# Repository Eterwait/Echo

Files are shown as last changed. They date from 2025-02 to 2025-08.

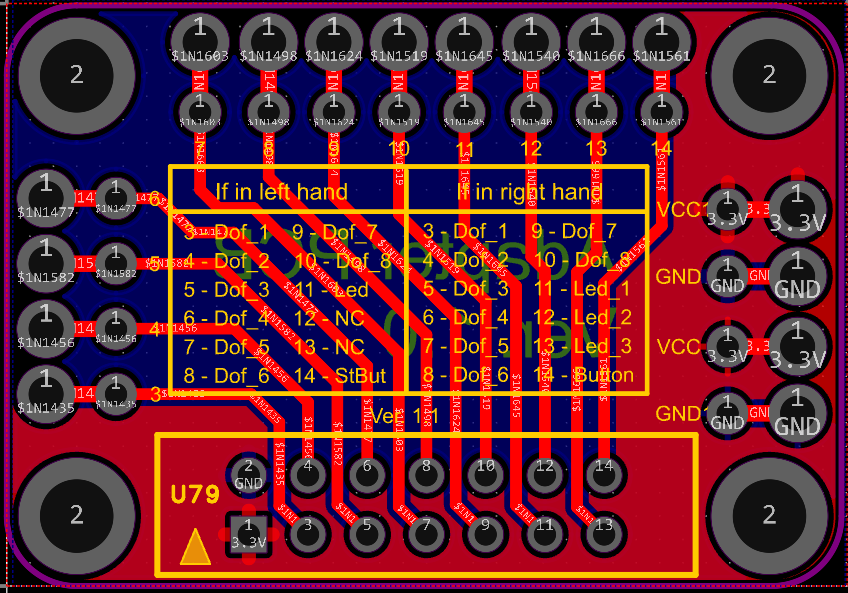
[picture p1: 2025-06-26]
Hardware/Commutation/Adapter_1.0/Adapter_1.0_schematic.PNG

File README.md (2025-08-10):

## Welcome to Echo!
This repository contains source materials for Echo, an open-source teleoperation system with force feedback.

Feel free to visit our [website](https://eterwait.github.io/Echo/) for more information!

### Repository content

- **Echo** - main code.
- **Hardware** - 3D models and electronic components.
- **STM32 code** - STM32 CubeIDE project files.
- **force_sensor_linearizer_rs485** - force sensor PCB code
- **Echo.bin** - ready-to-use microcontroller firmware. Download [Cube Programmer](https://www.st.com/en/development-tools/stm32cubeprog.html) and use it to upload the firmware to the board.
- **Echo.hex** - ready-to-use microcontroller firmware.

### Hardware & Assembly Tutorial

Echo is easy to put together with our [Hardware & Assembly Tutorial](https://eterwait.github.io/Echo/Hardware) videos and guide. Check it out to get started!

### Citation

```
@misc{bazhenov2025echoopensourcelowcostteleoperation,
      title={Echo: An Open-Source, Low-Cost Teleoperation System with Force Feedback for Dataset Collection in Robot Learning}, 
      author={Artem Bazhenov and Sergei Satsevich and Sergei Egorov and Dzmitry Tsetserukou},
      year={2025},
      eprint={2504.07939},
      archivePrefix={arXiv},
      primaryClass={cs.RO},
      url={https://arxiv.org/abs/2504.07939}, 
}
```

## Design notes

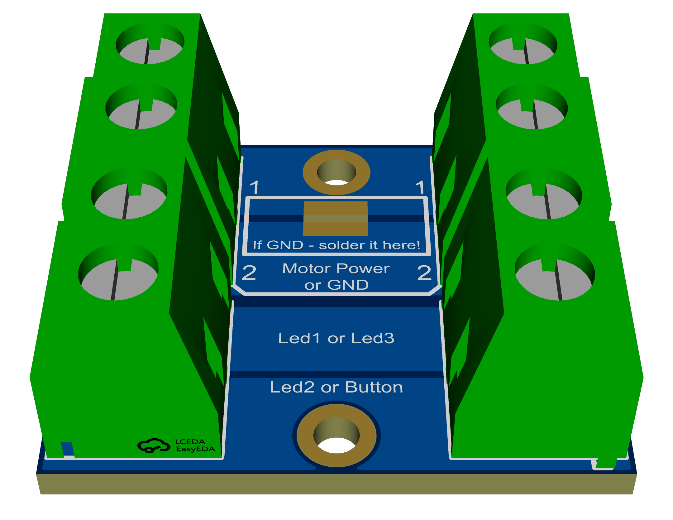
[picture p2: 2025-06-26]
Hardware/Commutation/Commutation_hand_1.0/Commutation_hand_1.0_side_view.png

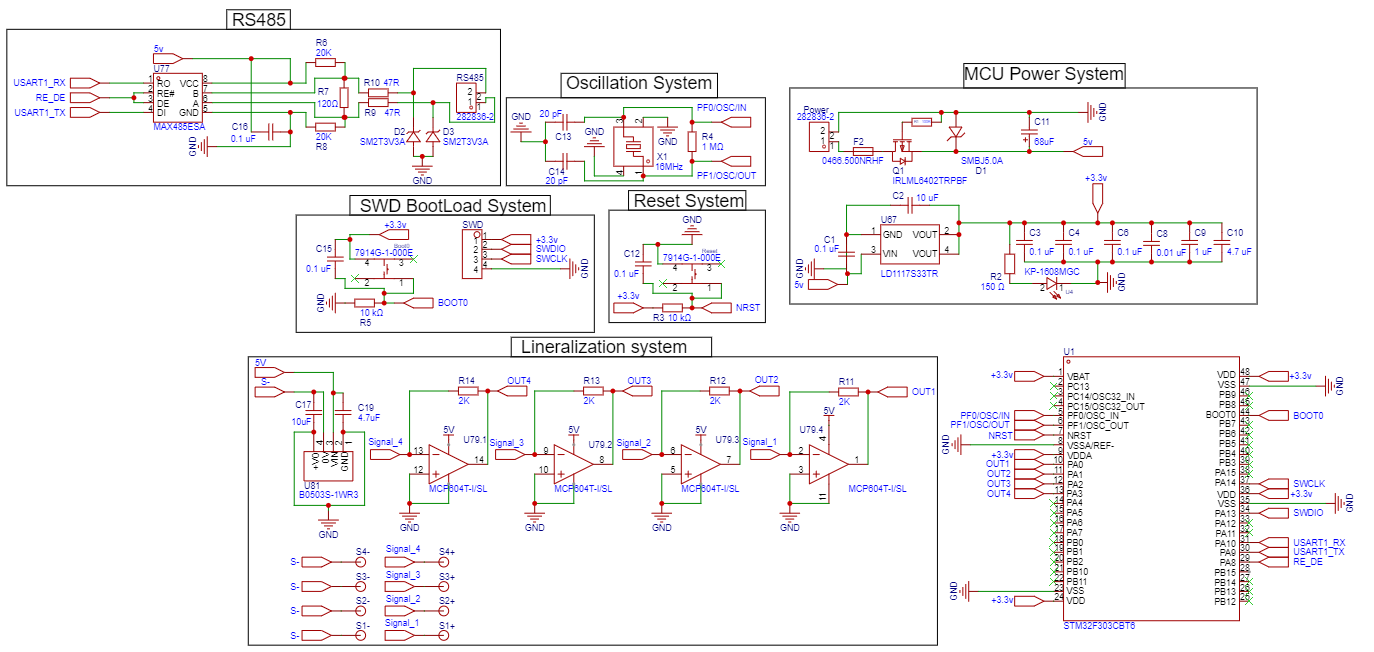
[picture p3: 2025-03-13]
Hardware/Force sensor PCB/Force sensor Schematics.png

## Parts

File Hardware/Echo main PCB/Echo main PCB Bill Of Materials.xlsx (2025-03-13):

No. | Vendor | Link | Device | Footprint | Quantity | Comment | Designator | Secondary Category | Name | Russian/Chinese Vendors | Link | Price rub
1 | DigiKey | https://www.digikey.com/en/products/detail/bourns-inc/7914G-1-000E/158358 | 7914G-1-000E | KEY-SMD_4P-L5.0-W5.0-P2.54-LS5.5-BL | 3 | 7914G-1-000E | Boot0,Boot1,Reset | Tactile Switches | 7914G-1-000E | chipdip | https://www.chipdip.ru/product/7914g-1-000 | 320
2 | Ali-Express | https://aliexpress.ru/item/1005004452143266.html?sku_id=12000029224903107 | GMD12095YB-3.3V | BUZ-TH_BD12.0-P7.60-D0.6-FD | 1 | GMD12095YB-3.3V | BUZZER | Buzzers | GMD12095YB-3.3V | Ali-Express | https://aliexpress.ru/item/1005004452143266.html?sku_id=12000029224903107 | 117
3 | Mouser | https://www.mouser.com/ProductDetail/Vishay-Vitramon/VJ0603Y104KXJAP | CAP_0603 GRM188R71H104JA93D | C0603 | 2 | 0.1 uF 16v | C1,C60 | Ceramic Capacitors MLCC - SMD/SMT | 0.1 uF 16v | chipdip | https://www.chipdip.ru/product/grm188r71h104ja93d | 6
4 | Mouser | https://www.mouser.com/ProductDetail/KYOCERA-AVX/TAJE227K016RNJ?qs=fdqkYiOtZpcgegJ8JKuPSw%3D%3D | TAJE227K016RNJ | CASE-E_7343 | 2 | 220 uF 16v | C2,C3 | Tantalum Capacitors | 220 uF 16v | chipdip | https://www.chipdip.ru/product/taje227k016rnj-avx | 250
5 | Mouser | https://www.mouser.com/ProductDetail/KYOCERA-AVX/TAJB226K016RNJ?qs=mgX5NEyWO4SD2hYJZOOvhw%3D%3D | TAJB226K016RNJ | CASE-B_3528 | 1 | 22 uF 10v | C4 | Tantalum Capacitors | 22 uF 10v | chipdip | https://www.chipdip.ru/product/tecap-22-mkf-16-v-tip-b-10 | 44
6 | Mouser | https://www.mouser.com/ProductDetail/KEMET/C0603X104K8RACTU | CAP_0603 GRM188R71H104JA93D | C0603 | 32 | 0.1 uF 10v | C5,C10,C11,C12,C13,C14,C18,C19,C20,C26,C27,C28,C29,C30,C31,C32,C33,C34,C35,C36,C37,C38,C39,C40,C41,C42,C43,C44,C51,C52,C68,C69 | Ceramic Capacitors MLCC - SMD/SMT | 0.1 uF 10v | chipdip | https://www.chipdip.ru/product/grm188r71h104ja93d | 6
7 | Mouser | https://www.mouser.com/ProductDetail/Murata-Electronics/GRM188R61A475KAAJD?qs=mJtAphxf33RijE30dSir3g%3D%3D | CAP_0603 GRM188R61A475K | C0603 | 2 | 4.7 uF 10v | C6,C66 | Ceramic Capacitors MLCC - SMD/SMT | 4.7 uF 10v | chipdip | https://www.chipdip.ru/product0/9000193550 | 15
8 | Mouser | https://www.mouser.com/ProductDetail/TDK/C1608X7R1A106M080AT | CAP_0603 GRM188Z71A106KA73D | C0603 | 1 | 10 uF 10v | C9 | Ceramic Capacitors MLCC - SMD/SMT | 10 uF 10v | chipdip | https://www.chipdip.ru/product0/9000502859 | 8
9 | Mouser | https://www.mouser.com/ProductDetail/KEMET/C0603C200K8HACTU?qs=W0yvOO0ixfG41DXbAfv7cA%3D%3D | CAP_0603 | C0603 | 2 | 20 pF 10v | C16,C17 | Ceramic Capacitors MLCC - SMD/SMT | 20 pF 10v | chipdip | https://www.chipdip.ru/product/grm1885c1h200j | 7
10 | Mouser | https://www.mouser.com/ProductDetail/Vishay-Sprague/293D104X9035A2TE3?qs=wgO0AD0o1vu82gSB7jpq2A%3D%3D | CAP_0603 293D104X9035A2TE3 | C0603,CASE-A_3216 | 4 | 0,1 uF 16v | C46,C47,C54,C55 | Tantalum Capacitors | 0,1 uF 16v | chipdip | https://www.chipdip.ru/product0/1654 | 32
11 | Newark | https://www.newark.com/kemet/c0603c224j4ractu/cap-0-22-f-16v-5-x7r-0603/dp/94Y9862 | CAP_0603 | C0603 | 2 | CBoot_0,22uF 16v | C48,C56 | Ceramic Capacitors MLCC - SMD/SMT | CBoot_0,22uF 16v | chipdip | https://www.chipdip.ru/product0/8013249347 | 2
12 | Newark | https://www.newark.com/kemet/c0603c103k4hactu/cap-0-01uf-16v-mlcc-0603-rohs/dp/66AJ6963 | CAP_0603 | C0603 | 2 | 0,01 uF 16v | C49,C57 | Ceramic Capacitors MLCC - SMD/SMT | 0,01 uF 16v | chipdip | https://www.chipdip.ru/product0/8022330951 | 5
13 | Newark | https://www.newark.com/murata/grm033r71a562ka01d/cap-5600pf-10v-mlcc-0201/dp/97AH9613 | CAP_0603 | C0603 | 2 | 5.6 nF 10v | C50,C58 | Ceramic Capacitors MLCC - SMD/SMT | 5.6 nF 10v | chipdip | https://www.chipdip.ru/product/grm188r71h562k | 7
14 | Newark | https://www.newark.com/murata/grm188c81c106ma73j/cap-10uf-16v-mlcc-0603-rohs-compliant/dp/64AJ4361 | CAP_0603 | C0603 | 1 | 10 uF 16v | C59 | Ceramic Capacitors MLCC - SMD/SMT | 10 uF 16v | chipdip | https://www.chipdip.ru/product0/9000388115 | 6
15 | Newark | https://www.newark.com/yageo/cc0603krx7r6bb104/cap-0-1uf-10v-mlcc-0603-rohs-compliant/dp/26AK1888 | CAP_0603 | C0603 | 4 | 0.1uF 10v | C61,C62,C63,C64 | Ceramic Capacitors MLCC - SMD/SMT | 0.1uF 10v | chipdip | https://www.chipdip.ru/product0/8005306866 | 29
16 | Newark | https://www.newark.com/kemet/c0603c105z8vactu/cap-1-f-10v-y5v-0603/dp/76Y2908 | CAP_0603 | C0603 | 1 | 1 uF 10v | C67 | Ceramic Capacitors MLCC - SMD/SMT | 1 uF 10v | chipdip | https://www.chipdip.ru/product/gcm188r71e105ka64d-murata | 28
17 | Ali-Express | https://aliexpress.ru/item/32878041549.html?sku_id=65528795603 | XT30PW-M30.G.Y | CONN-TH_XT30PW-M | 1 | XT30PW-M30.G.Y | CN1 | plug | XT30PW-M30.G.Y | Ali-Express | https://aliexpress.ru/item/32878041549.html?sku_id=65528795603 | 1200 | Total price rub:
18 | Mouser | https://www.mouser.com/ProductDetail/Bourns/SMCJ16A?qs=%252Bf8Cd6aE5byqCW8Yyl7Q2g%3D%3D | SMCJ16A_C310019 | SMC_L6.9-W5.9-LS7.9-RD | 1 | SMCJ16A | D1 | ESD and Surge Protection (TVS/ESD) | SMCJ16A | chipdip | https://www.chipdip.ru/product0/8011003304 | 140 | 11527
19 | Mouser | https://www.mouser.com/ProductDetail/STMicroelectronics/SM2T3V3A?qs=SoAZXCQuyY%2F4L%252BcP08CfZA%3D%3D | SM2T3V3A | DO-216AA_L1.9-W1.9-LS3.8-FD | 4 | SM2T3V3A | D3,D4,D5,D6 | TVS | SM2T3V3A | chipdip | https://www.chipdip.ru/product/sm2t3v3a-stm | 160
20 | Mouser | https://www.mouser.com/ProductDetail/Panjit/1N4148W_R1_00001?qs=sPbYRqrBIVnqVztCqPNVrw%3D%3D | 1N4148W_C143180 | SOD-123FL_L2.7-W1.6-LS3.8-RD | 4 | 1N4148W | D7,D8,D9,D10 | Switching Diodes | 1N4148W | chipdip | https://www.chipdip.ru/product/1n4148w-2 | 3
21 | Mouser | https://www.mouser.com/ProductDetail/Texas-Instruments/TPD2EUSB30DRTR?qs=%2Fqzd9s%252BcLd6bPJi5HXCDvw%3D%3D | TPD2EUSB30DRTR-TP | SOT-723-3_L1.2-W0.8-LS1.20-BR | 1 | TPD2EUSB30DRTR-TP | D15 | ESD and Surge Protection (TVS/ESD) | TPD2EUSB30DRTR-TP | chipdip | https://www.chipdip.ru/product0/8010090243 | 13
22 | Mouser | https://www.mouser.com/ProductDetail/Comchip-Technology/SS510-HF?qs=GBLSl2AkirsMVpU1ZRGkfw%3D%3D | SS510_C106905 | SMA_L4.4-W2.8-LS5.4-RD | 1 | SS510 | D16 | Schottky Diodes | SS510 | chipdip | https://www.chipdip.ru/product/ss510-umw | 11
23 | Ali-Express | https://aliexpress.ru/item/4001283958345.html?sku_id=12000043098655572 | HDR-M_2.54_1x4P | HDR-TH_4P-P2.54-V-M | 1 | HDR-M_2.54_1x4P | H1 | Pin Headers |  | Ali-Express | https://aliexpress.ru/item/4001283958345.html?sku_id=12000043098655572 | 63
24 | LCSC | https://www.lcsc.com/product-detail/IDC-Connectors_Ckmtw-Shenzhen-Cankemeng-B-3100S14P-A110_C146651.html | B-3100S14P-A110 | IDC-TH_310S-14P | 2 | B-3100S14P-A110 | Left_ADC,Right_ADC | IDC Connectors | B-3100S14P-A110 | chipdip | https://www.chipdip.ru/product/idcc-14ms | 26
25 | Mouser | https://www.mouser.com/ProductDetail/SparkFun/PRT-08432?qs=WyAARYrbSnYz%2FplK2qCI8A%3D%3D | 282836-2 | Screw terminal block 2-pin, 5mm CONN-TH_2P-P5.00_282836-2 | 6 | 282836-2 | Left_Motor_Power,POWER,POWER,Right_Motor_Power,RS485,RS485_2 | Screw Terminal Blocks | 282836-2 | chipdip | https://www.chipdip.ru/product/tyco-282836-2 | 80
26 | Newark | https://www.newark.com/tdk/mpz1608y151btd25/chip-bead-aec-q200-150-ohm-0603/dp/50AJ4286 | ERJ6ENF2053V,Res_0603 | R0603 | 5 | 150R | R1,R33,R34,R35,R49 | Chip Resistor - Surface Mount | 150R | chipdip | https://www.chipdip.ru/product0/8043206677 | 2
27 | Newark | https://www.newark.com/vishay/crcw06031m00fkta/res-thick-film-1m-1-0-1w-0603/dp/66F9077 | Res_0603 | R0603 | 1 | 1M | R2 | Chip Resistor - Surface Mount | 1M | chipdip | https://www.chipdip.ru/product/0.1w-0603-1-mom-1 | 6
28 | Newark | https://www.newark.com/vishay/crcw060310k0fkta/res-10k-1-0-1w-0603-thick-film/dp/22AC8032 | Res_0603 | R0603 | 7 | 10K | R3,R4,R5,R36,R38,R39,R41 | Chip Resistor - Surface Mount | 10K | chipdip | https://www.chipdip.ru/product/0.1w-0603-10-kom-5 | 6
29 | Newark | https://www.newark.com/yageo/rc0603fr-0720kl/res-20k-1-0-1w-0603-thick-film/dp/82AH8092 | Res_0603 | R0603 | 2 | 20K | R12,R14 | Chip Resistor - Surface Mount | 20K | chipdip | https://www.chipdip.ru/product/0.1w-0603-20-kom-1 | 6
30 | Newark | https://www.newark.com/murata/blm31pg121sn1l/ferrite-bead-120r-3-5a-1206/dp/02AC3396 | 1206W4J0121T5E | R1206 | 1 | 120R | R13 | Chip Resistor - Surface Mount | 120R | chipdip | https://www.chipdip.ru/product/0.25w-1206-120-om-1 | 6
31 | Newark | https://www.newark.com/vishay/crcw060347r0fkea/res-thick-film-47r-1-0-1w-0603/dp/72M6842 | Res_0603 | R0603 | 2 | 47R | R15,R16 | Chip Resistor - Surface Mount | 47R | chipdip | https://www.chipdip.ru/product/0.1w-0603-47-om-1 | 6
32 | Newark | https://www.newark.com/vishay/crcw060310r0jnea/res-thick-film-10r-5-0-1w-0603/dp/59M6762 | Res_0603 | R0603 | 16 | 10R | R17,R18,R19,R20,R21,R22,R23,R24,R25,R26,R27,R28,R29,R30,R31,R32 | Chip Resistor - Surface Mount | 10R | chipdip | https://www.chipdip.ru/product/0.1w-0603-10-om-1 | 6
33 | Newark | https://www.newark.com/vishay/crcw0603100rfkta/res-thick-film-100r-1-0-1w-0603/dp/66F9065 | Res_0603 | R0603 | 2 | 100R | R37,R40 | Chip Resistor - Surface Mount | 100R | chipdip | https://www.chipdip.ru/product/0.1w-0603-100-om-1 | 6
34 | Newark | https://www.newark.com/yageo/rt0603drd075k1l/res-5k1-0-5-0-1w-0603-thin-film/dp/82AH8969 | Res_0603 | R0603 | 1 | 5,1K | R42 | Chip Resistor - Surface Mount | 5,1K | chipdip | https://www.chipdip.ru/product/0.1w-0603-5.1-kom-1 | 6
35 | Newark | https://www.newark.com/te-connectivity/cpf0603b24re1/surface-mount-thin-film-resistor/dp/95W6640 | Res_0603 | R0603 | 4 | 24R | R43,R44,R45,R46 | Chip Resistor - Surface Mount | 24R | chipdip | https://www.chipdip.ru/product/0.1w-0603-24-om-1 | 6
36 | Newark | https://www.newark.com/vishay/crcw0603330rjnea/res-thick-film-330r-5-0-1w-0603/dp/59M6805 | Res_0603 | R0603 | 1 | 330R | R47 | Chip Resistor - Surface Mount | 330R | chipdip | https://www.chipdip.ru/product/0.1w-0603-330-om-1 | 6
37 | Newark | https://www.newark.com/vishay/rca06031k00fkea/res-aec-q200-thick-film-1k-1-0603/dp/98Y2317 | Res_0603 | R0603 | 1 | 1K | R48 | Chip Resistor - Surface Mount | 1K | chipdip | https://www.chipdip.ru/product/0.1w-0603-1-kom-5 | 6
38 | Ali-Express | https://aliexpress.ru/item/1005006849944988.html?sku_id=12000038510475301 | UWF1205S-3WR3_C41355411 | PWRM-TH_UWFXXXXS-3WR3 | 1 | UWF1205S-3WR3 | U4 | Isolated Power Modules | UWF1205S-3WR3 | chipdip | https://www.chipdip.ru/product/uwf1205s-3wr3 | 770
39 | Mouser | https://www.mouser.com/ProductDetail/STMicroelectronics/LD1117S33TR?qs=edoyzKMbmhntQZx4BFmoqw%3D%3D | LD1117S33TR | SOT-223_L6.5-W3.5-P2.30-LS7.0-BR | 2 | LD1117S33TR | U5,U79 | Voltage Regulators - Linear, LDO | LD1117S33TR | chipdip | https://www.chipdip.ru/product/ld1117s33tr | 31
40 | Newark | https://www.newark.com/kingbright/kp-1608mgc/led-green-0-8mm-x-1-2mm-70mcd/dp/38K3371 | KP-1608MGC | LED0603-RD_GREEN | 2 | KP-1608MGC | U6,U86 |  | KP-1608MGC | chipdip | https://www.chipdip.ru/product/kp-1608mgc | 66
41 | Mouser | https://www.mouser.com/ProductDetail/Analog-Devices-Maxim-Integrated/MAX485ESA%2b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 | MAX485ESA_C5279041 | SOIC-8_L4.9-W3.9-P1.27-LS6.0-BL | 1 | MAX485ESA | U8 | RS-485 / RS-422 ICs | MAX485ESA | chipdip | https://www.chipdip.ru/product/max485esa-umw | 46
42 | Mouser | https://www.mouser.com/ProductDetail/Toshiba/TBD62003AFGEL?qs=fSnNYG2PaKIjjnu%2FCiwe6Q%3D%3D | TBD62003AFG,EL | SOP-16_L10.0-W4.4-P1.27-LS6.3-BL | 1 | TBD62003AFG,EL | U9 | Power Distribution Switches | TBD62003AFG,EL | chipdip | https://www.chipdip.ru/product/tbd62003afg-el | 250
43 | Mouser | https://www.mouser.com/ProductDetail/Texas-Instruments/ISO7740DWR?qs=dSktwyqbRaUgeH6KogaGsw%3D%3D | ISO7740DWR | SOIC-16_L10.3-W7.5-P1.27-LS10.3-BL | 2 | ISO7740DWR | U10,U12 | Digital Isolators | ISO7740DWR | chipdip | https://www.chipdip.ru/product0/8024963566 | 250
44 | Mouser | https://www.mouser.com/ProductDetail/STMicroelectronics/L6205PD?qs=yAkVQ3mwCG0m75OpqT8zRw%3D%3D | L6205PD | POWERSO20_L15.9-W11.0-P1.27-LS14.2-BL-EP | 2 | L6205PD | U11,U13 |  | L6205PD | chipdip | https://www.chipdip.ru/product/l6205pd | 960
45 | Mouser | https://www.mouser.com/ProductDetail/STMicroelectronics/STM32F401RET6?qs=s5SkPsIz108eLldhTu8INg%3D%3D | STM32F401RET6 | LQFP-64_L10.0-W10.0-P0.50-LS12.0-BL | 1 | STM32F401RET6 | U78 | Microcontrollers (MCU/MPU/SOC) | STM32F401RET6 | chipdip | https://www.chipdip.ru/product/stm32f401ret6-2 | 670
46 | Mouser | https://www.mouser.com/ProductDetail/Analog-Devices/ADUM4160BRWZ-RL?qs=WIvQP4zGaniP0FyiFgFlCw%3D%3D | ADUM4160BRWZ-RL_C57791 | SOIC-16_L10.3-W7.5-P1.27-LS10.3-BL | 1 | ADUM4160BRWZ-RL | U83 | Isolated USB ICs | ADUM4160BRWZ-RL | chipdip | https://www.chipdip.ru/product/adum4160brwz | 1590
47 | Mouser | https://www.mouser.com/ProductDetail/Littelfuse/045106.3MRL?qs=qI%252BDxnNls182PnT2BcnTWA%3D%3D | 045106.3MRL | FUSE-SMD_L6.1-W2.6 | 1 | 045106.3MRL | U84 | Disposable fuses | 045106.3MRL | chipdip | https://www.chipdip.ru/product0/9000463134 | 16
48 | Mouser | https://www.mouser.com/ProductDetail/Analog-Devices-Maxim-Integrated/MAX6817EUT%2bT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 | MAX6817EUT+T | SOT-23-6_L2.9-W1.6-P0.95-LS2.8-BL | 1 | MAX6817EUT+T | U85 | Interface - Specialized | MAX6817EUT+T | chipdip | https://www.chipdip.ru/product0/8345478677 | 320
49 | Ali-Express | https://aliexpress.ru/item/1005007524394521.html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 | USB-TYPE-C-020 | USB-SMD_USB-TYPE-C-020 | 1 | USB-TYPE-C-020 | USB2 | USB Connectors | USB-TYPE-C-020 | Ali-Express | https://aliexpress.ru/item/1005007524394521.html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 | 179
50 | Newark | https://www.newark.com/abracon/abm3baig-16-000mhz-12-d4z-t/crystal-aec-q200-16mhz-12pf-5x3/dp/94AC3695 | SJK 16.000 MHz, smd 5×3.2 mm or HY16MSMD50324POB1R10 or ABM3BAIG-16.000MHZ-12-D4Z-T | CRYSTAL-SMD_4P-L5.0-W3.2-BL | 1 | 16MHz | X1 | Crystals Oscillators | 16MHz | chipdip | https://www.chipdip.ru/product0/9001627012 | 40

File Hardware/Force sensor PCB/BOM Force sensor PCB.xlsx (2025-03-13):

No. | Quantity | Comment | Designator | Primary Category | Secondary Category | Device | Name | Footprint
1 | 2 | 7914G-1-000E | Boot0,Reset | Switches | Tactile Switches | 7914G-1-000E | 7914G-1-000E | KEY-SMD_4P-L5.0-W5.0-P2.54-LS5.5-BL
2 | 7 | 0.1 uF | C1,C3,C4,C6,C12,C15,C16 | Capacitors | Multilayer Ceramic Capacitors MLCC - SMD/SMT | CAP_0603 | 0.1 uF | C0603
3 | 2 | 10 uF | C2,C17 | Capacitors | Multilayer Ceramic Capacitors MLCC - SMD/SMT | CAP_0603 | 10 uF | C0603
4 | 1 | 0.01 uF | C8 | Capacitors | Multilayer Ceramic Capacitors MLCC - SMD/SMT | CAP_0603 | 0.01 uF | C0603
5 | 1 | 1 uF | C9 | Capacitors | Multilayer Ceramic Capacitors MLCC - SMD/SMT | CAP_0603 | 1 uF | C0603
6 | 2 | 4.7 uF | C10,C19 | Capacitors | Multilayer Ceramic Capacitors MLCC - SMD/SMT | CAP_0603 | 4.7 uF | C0603
7 | 1 | 68 uF | C11 | Capacitors | Tantalum Capacitors | TLJB227M006R0500 | 68 uF | CASE-B_3528
8 | 2 | 20 pF | C13,C14 | Capacitors | Multilayer Ceramic Capacitors MLCC - SMD/SMT | CAP_0603 | 20 pF | C0603
9 | 1 | SMBJ5.0A | D1 | Circuit Protection | ESD and Surge Protection (TVS/ESD) | SMBJ5.0A_C782420 | SMBJ5.0A | SMB_L4.3-W3.6-LS5.4-RD
10 | 2 | SM2T3V3A | D2,D3 | TVS/Fuse/Board Level Protection | TVS | SM2T3V3A | SM2T3V3A | DO-216AA_L1.9-W1.9-LS3.8-FD
11 | 1 | 0466.500NRHF | F2 | Circuit Protection | Disposable fuses | 0466.500NRHF | 0466.500NRHF | F1206
12 | 2 | 282836-2 | Power,RS485 | Connectors | Screw Terminal Blocks | 282836-2 | 282836-2 | CONN-TH_2P-P5.00_282836-2
13 | 1 | IRLML6402TRPBF | Q1 | Transistors/Thyristors | MOSFETs | IRLML6402TRPBF_C2593 | IRLML6402TRPBF | SOT-23-3_L2.9-W1.6-P1.90-LS2.8-BR
14 | 1 | 100R | R1 | Resistors | Chip Resistor - Surface Mount | Res_0603 | 100R | R0603
15 | 1 | 150 Ω | R2 | Resistors | Chip Resistor - Surface Mount | ERJ6ENF2053V | 150 Ω | R0805
16 | 2 | 10K | R3,R5 | Resistors | Chip Resistor - Surface Mount | Res_0603 | 10K | R0603
17 | 1 | 1M | R4 | Resistors | Chip Resistor - Surface Mount | Res_0603 | 1M | R0603
18 | 2 | 20K | R6,R8 | Resistors | Chip Resistor - Surface Mount | Res_0603 | 20K | R0603
19 | 1 | 120R | R7 | Resistors | Chip Resistor - Surface Mount | 1206W4J0121T5E | 120R | R1206
20 | 2 | 47R | R9,R10 | Resistors | Chip Resistor - Surface Mount | Res_0603 | 47R | R0603
21 | 4 | 2K | R11,R12,R13,R14 | Resistors | Chip Resistor - Surface Mount | Res_0603 | 2K | R0603
22 | 8 | robust_pin | S1+,S1-,S2+,S2-,S3+,S3-,S4+,S4- |  |  | robust_pin |  | robust_pin
23 | 1 | HDR-M_2.54_1x4P | SWD | Connectors | Pin Headers | HDR-M_2.54_1x4P |  | HDR-TH_4P-P2.54-V-M
24 | 1 | STM32F303CBT6 | U1 | Embedded Processors & Controllers | Microcontrollers (MCU/MPU/SOC) | STM32F303CBT6 | STM32F303CBT6 | LQFP-48_L7.0-W7.0-P0.50-LS9.0-BL
25 | 1 | KP-1608MGC | U4 |  |  | KP-1608MGC | KP-1608MGC | LED0603-RD_GREEN
26 | 1 | LD1117S33TR | U67 | Power Management (PMIC) | Voltage Regulators - Linear, Low Drop Out (LDO) Regulators | LD1117S33TR | LD1117S33TR | SOT-223_L6.5-W3.5-P2.30-LS7.0-BR
27 | 1 | MAX485ESA | U77 | Interface | RS-485 / RS-422 ICs | MAX485ESA_C5279041 | MAX485ESA | SOIC-8_L4.9-W3.9-P1.27-LS6.0-BL
28 | 1 | MCP604T-I/SL | U79 | Amplifiers/Comparators | Operational Amplifier | MCP604T-I/SL | MCP604T-I/SL | SOIC-14_L8.7-W3.9-P1.27-LS6.0-BL
29 | 1 | B0503S-1WR3 | U81 |  |  | B0503S-1WR3 | B0503S-1WR3 | PWRM-TH_B0503S-1WR2
30 | 1 | 16MHz | X1 | Crystals, Oscillators, Resonators | Crystals | HY13MSMD50324POB1R10 | 16MHz | CRYSTAL-SMD_4P-L5.0-W3.2-BL

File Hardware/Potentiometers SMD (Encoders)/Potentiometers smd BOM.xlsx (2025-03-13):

No. | Vendor | Link | Quantity | Comment | Designator | Secondary Category | Footprint | Device | Name | Russian/Chinese Vendor | Link
1 | Mouser | https://www.mouser.com/ProductDetail/KYOCERA-AVX/0603ZG104ZAT2A?qs=XWDBCzcA0Tke70DI9cEVbA%3D%3D | 2 | 0.1 uF 10v | C1,C2 | Ceramic Capacitors MLCC - SMD/SMT | C0603 | 0.1uF X7R 16V 10% 0603 | 0.1 uF 10v | chip-dip | https://www.chipdip.ru/product0/9000591947
2 | Mouser | https://www.mouser.com/ProductDetail/TDK/C1608X7R1A106M080AT?qs=Vi0JKjFBtYn5h0pkhcUtLQ%3D%3D | 1 | 10 uF 10v | C3 | Ceramic Capacitors MLCC - SMD/SMT | C0603 | GRM188Z71A106KA73D | 10 uF 10v | chip-dip | https://www.chipdip.ru/product0/9000502859
3 | Ali-Express | https://aliexpress.ru/item/32878041549.html?sku_id=65528795603 | 1 | MR30PW-M20.G.Y | CN1 | Plug | robust_pin | MR30PW-M20.G.Y | MR30PW-M20.G.Y | Ali-Express | https://aliexpress.ru/item/32878041549.html?sku_id=65528795603
4 | Ali-Express | https://aliexpress.ru/item/1005007976685484.html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 | 1 | SV01A103AEA01R00 | U1 | Position Sensors | SENSOR-SMD_SV01A103AEA01R00 | SV01A103AEA01R00 | SV01A103AEA01R00 | Ali-Express | https://aliexpress.ru/item/1005007976685484.html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
5 | Mouser | https://www.mouser.com/ProductDetail/Microchip-Technology/MCP6001RT-I-OT?qs=Sez7gRs8XSW1kL18gOm8pA%3D%3D | 1 | MCP6001RT-I/OT | U2 | Operational Amplifier | SOT-23-5_L3.0-W1.7-P0.95-LS2.8-BR | MCP6001RT-I/OT | MCP6001RT-I/OT | chip-dip | https://www.chipdip.ru/product/mcp6001rt-i-ot-microchip

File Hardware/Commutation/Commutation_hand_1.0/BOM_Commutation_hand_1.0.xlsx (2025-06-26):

No. | Quantity | Comment | Designator | Footprint
1 | 4 | 282836-2 | 1,1*,2,2* | CONN-TH_2P-P5.00_282836-2

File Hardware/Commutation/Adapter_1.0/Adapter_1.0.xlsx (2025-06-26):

No. | Quantity | Comment | Designator | Footprint
1 | 1 | DS1018-142BX | U79 | HDR-TH_14P-P2.54_CONNFLY_DS1018-142BX

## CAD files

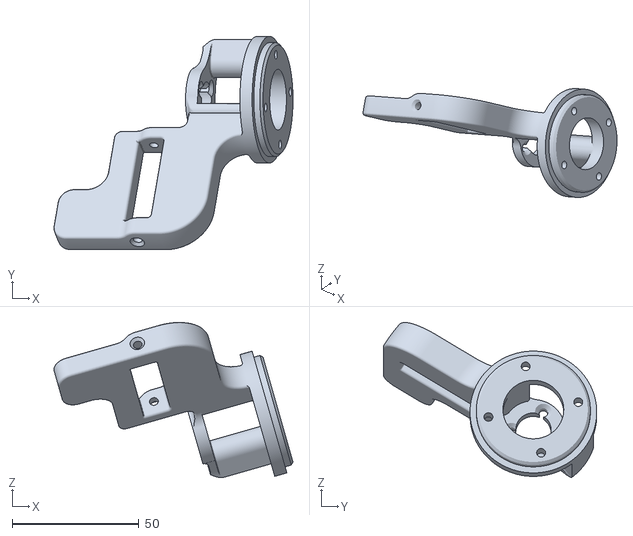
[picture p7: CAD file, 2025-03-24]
Hardware/3D models/STL files/ECHO.000.024.001 - Trigger.stl
94.3 x 84.2 x 61.2

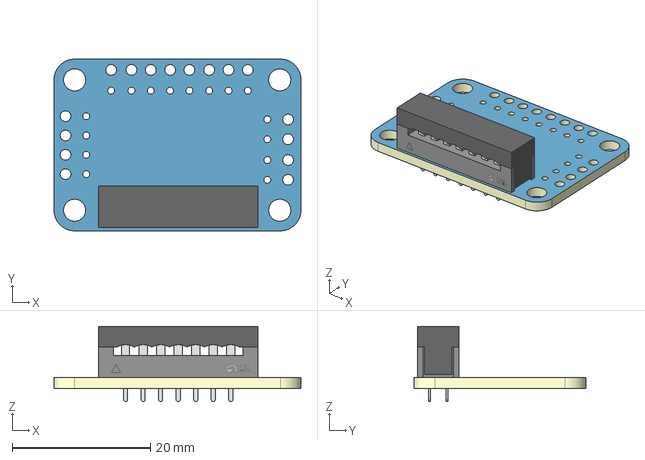
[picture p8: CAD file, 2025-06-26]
Hardware/Commutation/Adapter_1.0/Adapter_1.0.step
35.8 x 24.9 x 10.9 mm
Board

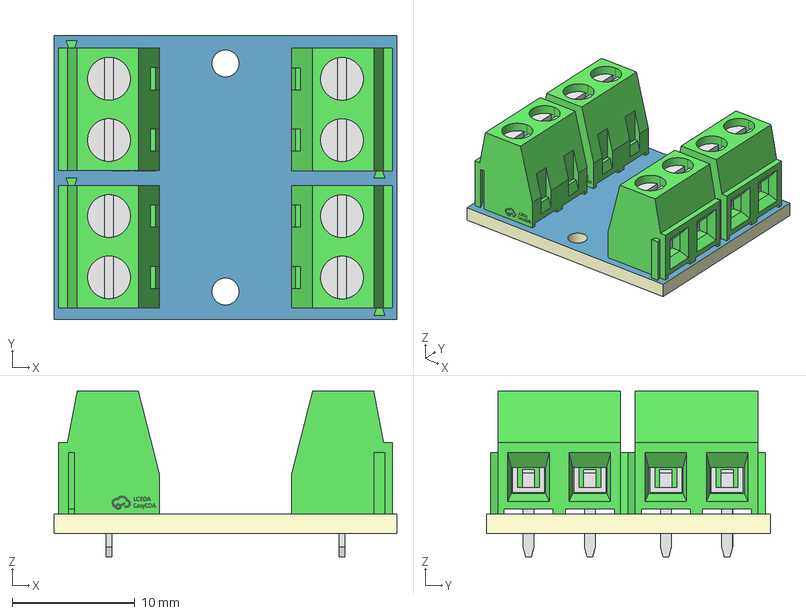
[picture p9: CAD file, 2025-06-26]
Hardware/Commutation/Commutation_hand_1.0/Commutation_hand_1.0.step
28.0 x 23.2 x 13.5 mm
Board

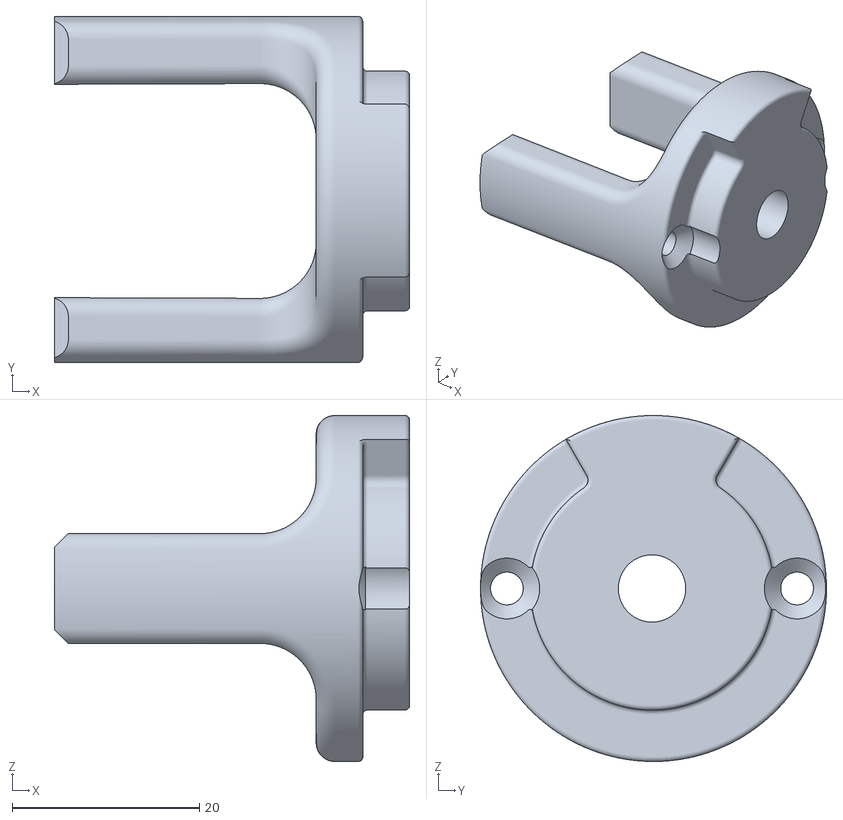
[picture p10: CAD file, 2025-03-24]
Hardware/3D models/STL files/ECHO.000.001.005 - Bracket.stl
38.0 x 37.0 x 37.0

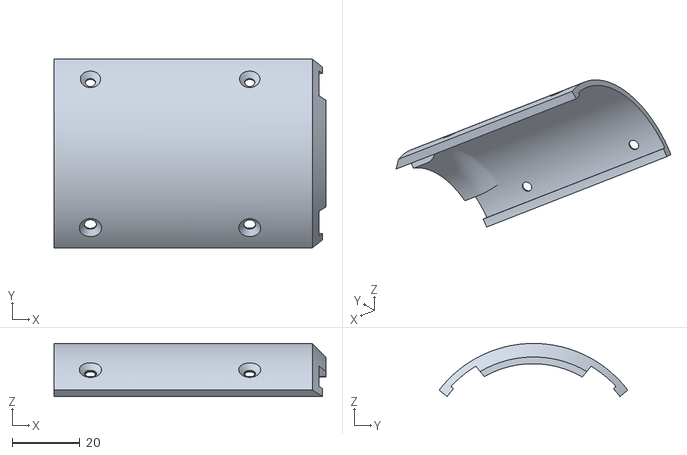
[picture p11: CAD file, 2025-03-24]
Hardware/3D models/STL files/ECHO.000.001.001 - Wall.stl
80.2 x 55.7 x 15.7

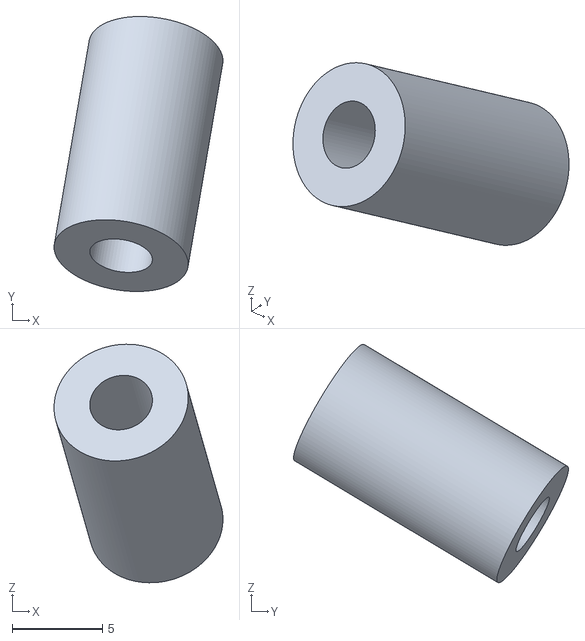
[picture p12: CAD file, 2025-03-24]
Hardware/3D models/STL files/ECHO.000.034.002 - Insert.stl
9.34 x 15.2 x 13.2

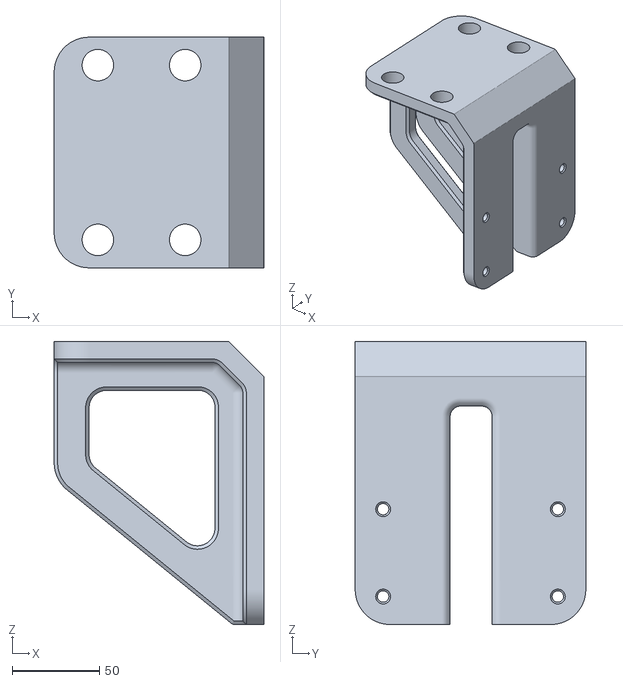
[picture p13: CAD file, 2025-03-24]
Hardware/3D models/STL files/ECHO.000.000.010 - Bracket to the welding table.stl
120.0 x 132.0 x 162.0

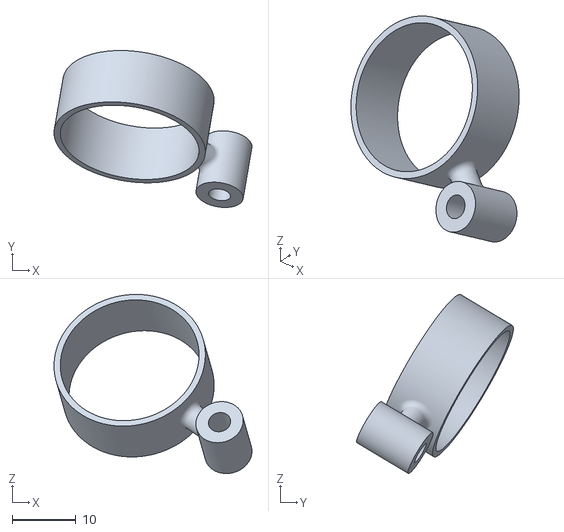
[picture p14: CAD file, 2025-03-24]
Hardware/3D models/STL files/ECHO.000.034.001 - Thimble D22 mm.stl
31.1 x 24.6 x 28.1

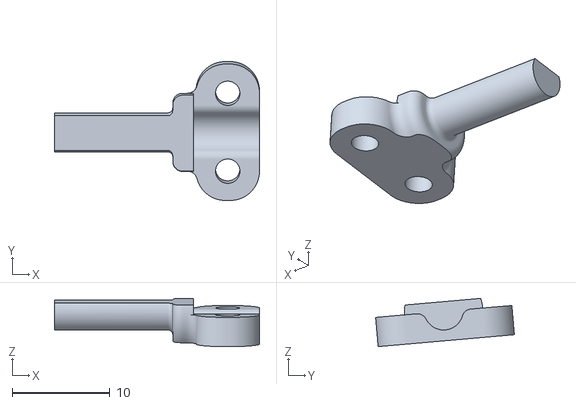
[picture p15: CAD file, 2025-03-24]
Hardware/3D models/STL files/ECHO.000.006.003 - Tongue.stl
21.0 x 14.2 x 4.93

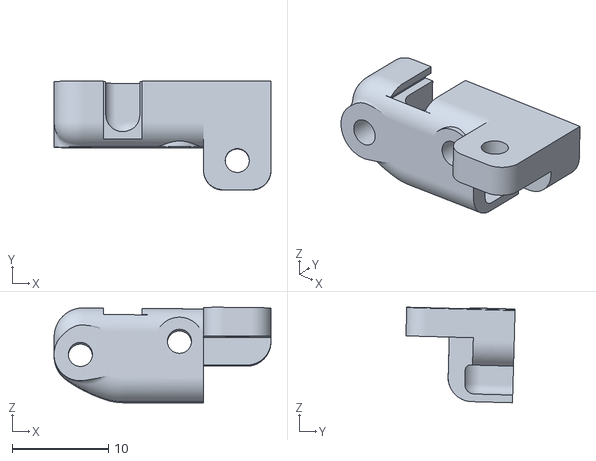
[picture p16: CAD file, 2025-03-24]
Hardware/3D models/STL files/ECHO.000.007.002 - Protector.stl
22.5 x 11.3 x 9.92

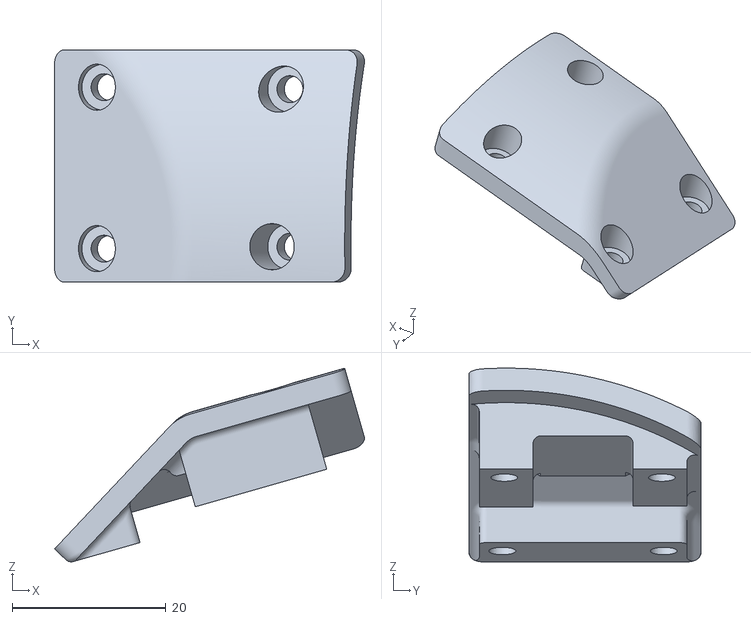
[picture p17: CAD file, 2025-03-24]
Hardware/3D models/STL files/ECHO.000.004.005 - Cup.stl
40.3 x 30.2 x 25.2

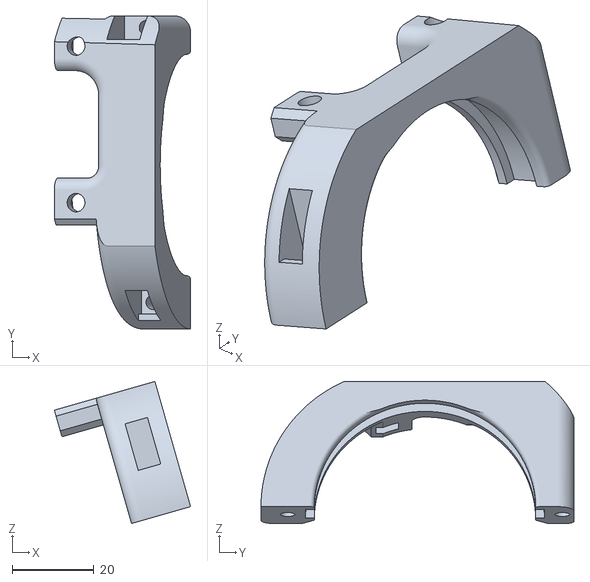
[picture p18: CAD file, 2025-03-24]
Hardware/3D models/STL files/ECHO.000.024.005 -Bearing holder.stl
33.2 x 76.4 x 34.6

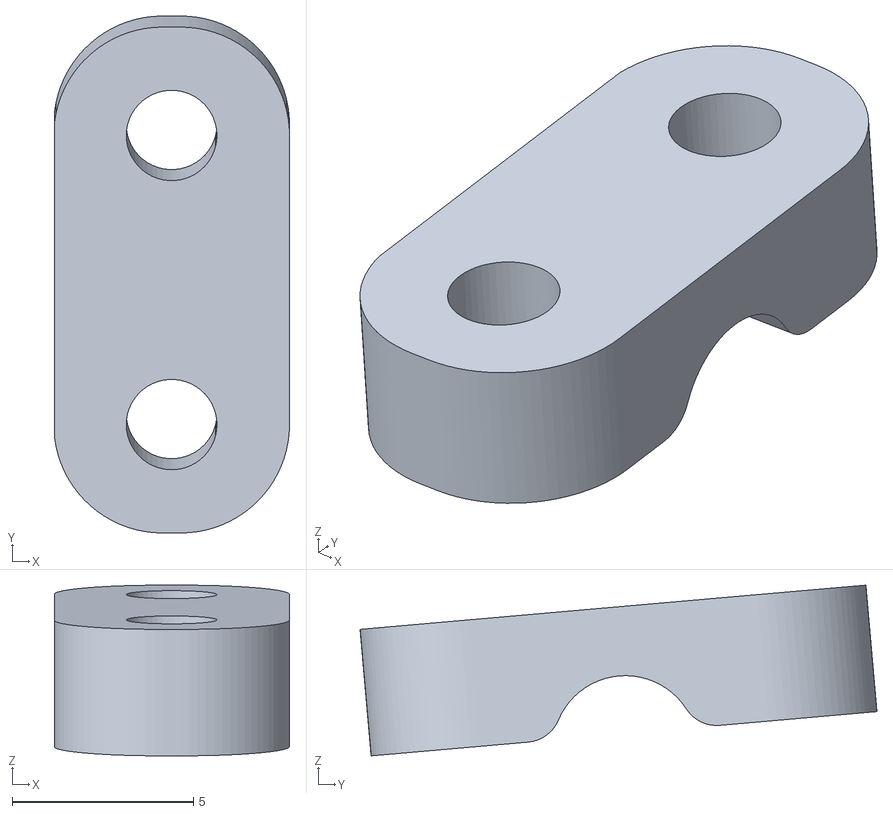
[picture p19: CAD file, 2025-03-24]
Hardware/3D models/STL files/ECHO.000.006.001 - Plate_bk.stl
6.48 x 14.3 x 4.71

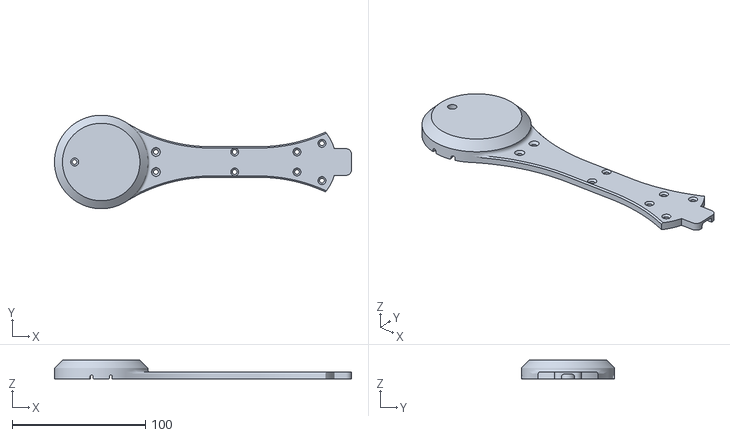
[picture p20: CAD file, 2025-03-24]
Hardware/3D models/STL files/ECHO.000.003.004 - Cup.stl
222.5 x 70.0 x 14.0

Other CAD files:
Hardware/3D models/STL files/ECHO.000.007.001 - Protector.stl
Hardware/3D models/STL files/ECHO.000.024.002 - Bracket.stl
Hardware/3D models/STL files/ECHO.000.004.008 -Wire channel.stl
Hardware/3D models/STL files/ECHO.000.006.002 - Plate.stl
Hardware/3D models/NX files/1111.100.000 - Aluminum frame.prt
Hardware/3D models/NX files/1111.100.002 - Aluminum profile.prt
Hardware/3D models/NX files/1111.100.004 - Aluminum profile.prt
Hardware/3D models/NX files/1111.100.005 - Aluminum profile.prt
Hardware/3D models/NX files/1111.200.000 - Bracket for camera.prt
Hardware/3D models/NX files/1111.200.001 - Bracket.prt
Hardware/3D models/NX files/1111.200.002 - Bracket.prt
Hardware/3D models/NX files/2222.000.000.000 - Force-Sensor-Equipped Gripper.prt
Hardware/3D models/NX files/2222.000.000.002 - Link.prt
Hardware/3D models/NX files/2222.000.000.002 - Pad.prt
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

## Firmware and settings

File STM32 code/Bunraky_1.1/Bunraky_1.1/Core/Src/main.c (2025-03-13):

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
/* Includes ------------------------------------------------------------------*/
#include "main.h"
#include "adc.h"
#include "crc.h"
#include "tim.h"
#include "usart.h"
#include "usb_device.h"
#include "gpio.h"

/* USER CODE BEGIN Includes */
#include "bunraky_lib.h"
#include "globals.h"
#include <stdint.h>
#include "usbd_cdc_if.h"
/* USER CODE END Includes */


void SystemClock_Config(void);
/**
  * @brief  The application entry point.
  * @retval int
  */
int main(void)
{
  /* MCU Configuration--------------------------------------------------------*/

  /* Reset of all peripherals, Initializes the Flash interface and the Systick. */
  HAL_Init();

  /* Configure the system clock */
  SystemClock_Config();

  /* Initialize all configured peripherals */
  MX_GPIO_Init();
  MX_ADC1_Init();
  MX_CRC_Init();
  MX_TIM2_Init();
  MX_TIM3_Init();
  MX_USART6_UART_Init();
  MX_USB_DEVICE_Init();
  /* USER CODE BEGIN 2 */
  	uint32_t crc_test_value = 462;



	// Start Tim 2 to work, it will produce right motor PWM
	LL_TIM_CC_EnableChannel(TIM2, LL_TIM_CHANNEL_CH1);
	LL_TIM_EnableCounter(TIM2);

	// Set En and Dir pins for right motor
	LL_GPIO_SetOutputPin(En_right_motor_GPIO_Port, En_right_motor_Pin);
	LL_GPIO_ResetOutputPin(Dir_right_motor_GPIO_Port, Dir_right_motor_Pin);

	// Set PWM for right motor to 0 (equal ZERO current)
	LL_TIM_OC_SetCompareCH1(TIM2,0);



	// Allow Tim 3 to work, it will produce left motor PWM
	LL_TIM_CC_EnableChannel(TIM3, LL_TIM_CHANNEL_CH1);
	LL_TIM_EnableCounter(TIM3);

	// Set En and Dir pins for left motor
	LL_GPIO_SetOutputPin(En_left_motor_GPIO_Port, En_left_motor_Pin);
	LL_GPIO_ResetOutputPin(Dir_left_motor_GPIO_Port, Dir_left_motor_Pin);

	// Set PWM for left motor to 0 (equal ZERO current)
	LL_TIM_OC_SetCompareCH1(TIM3,0);



	// Allow USART 6 to work
	NVIC_EnableIRQ(USART6_IRQn);

	//  LL_USART_Enable(USART6);
	USART6->CR1 |= USART_CR1_TE | USART_CR1_RE;
	LL_USART_EnableIT_RXNE(USART6);
	LL_USART_EnableIT_ERROR(USART6);

	LL_GPIO_ResetOutputPin(RE_DE_GPIO_Port, RE_DE_Pin); // Set MAX485 to Rx mode

//    LL_TIM_EnableIT_UPDATE(TIM2); // Start timer 2 for interruption each 35 ms for buzzers
//    LL_TIM_EnableCounter(TIM2);   // Start timer 2

	// Load calibration values from flash
	uint8_t init_load_calibration_error = init_load_calibration_values(); // if 1 == some problems
	uint32_t error = 0;
	uint32_t error_zero_dof_6 = 0;
	uint32_t error_zero_dof_7 = 0;
	uint32_t error_zero_dof_8 = 0;
	uint32_t stop_motor_counter = 0;

	//	uint8_t count_write_flash = sizeof(my_array) / sizeof(my_array[0]);
	//	uint32_t error = flash_write_words(FLASH_SECTOR_6, ADDR_FLASH_SECTOR_6, CCW_limits_uint32_flash, count_write_flash);
	//	uint32_t error = flash_write_words(FLASH_SECTOR_6, ADDR_FLASH_SECTOR_6, CW_limits_uint32_flash, count_write_flash);
	LL_GPIO_SetOutputPin(Sense_Lvl_1_GPIO_Port, Sense_Lvl_1_Pin);
	start_melody();

  /* USER CODE END 2 */

  /* Infinite loop */
  /* USER CODE BEGIN WHILE */
  while (1)
  {
	  LL_mDelay(1);

//	  readADCchannels();
//	  is_min_max_calibrated();
//	  calibration_ADC_values();

//	  USB_Rx_buffer[0]='r'; // Command to calibration
//	  LL_mDelay(2000);
//	  USB_Rx_buffer[0]='c'; // Command to calibration
//	  USB_Rx_buffer[1]='l'; // Left arm choice
//	  USB_Rx_buffer[2]='6'; // DoF mode
//	  USB_Rx_buffer[3]='1'; // DoF to calibrate
//	  USB_Rx_buffer[4]='0'; // Min Max choice
	  switch(USB_Rx_buffer[0])
		  {
	  	  	 case 'c': // command to calibration
	  	  		 switch(USB_Rx_buffer[1])
	  	  		 {
	  	  		 	 case 'l': // left arm choice
	  	  		 		 switch(USB_Rx_buffer[2])
	  	  		 		 {
							 case'6': //  6 DoF mode (without gripper) choice
								 switch(USB_Rx_buffer[3])
								 {
									 case '1':  //  DoF to calibrate choice
										 // The first parameter is the CCW or CW command, the second parameter is the DoF number
										 process_calibration(USB_Rx_buffer[4], 1);
									 break;

									 case '2':
										 process_calibration(USB_Rx_buffer[4], 2);
									 break;

									 case '3':
										 process_calibration(USB_Rx_buffer[4], 3);
									 break;

									 case '4':
										 process_calibration(USB_Rx_buffer[4], 4);
									 break;

									 case '5':
										 process_calibration(USB_Rx_buffer[4], 5);
									 break;

									 case '6':
										 error_zero_dof_8 = wrote_zero_to_dof(7);
										 error_zero_dof_8 = wrote_zero_to_dof(8);
										 process_calibration(USB_Rx_buffer[4], 6);

									 break;
								 }
								 break;

	  	  		 		 	 case'7': //  7 DoF mode choice
	  		  	  		 		 switch(USB_Rx_buffer[3])
	  		  	  		 		 {
	  		  	  		 		 	 case '1':
	  		  	  		 		 		 process_calibration(USB_Rx_buffer[4], 1);
	  		  	  		 		 	 break;

	  		  	  		 		 	 case '2':
	  		  	  		 		 		 process_calibration(USB_Rx_buffer[4], 2);
	  		  	  		 		 	 break;

	  		  	  		 		 	 case '3':
	  		  	  		 		 		 process_calibration(USB_Rx_buffer[4], 3);
	  		  	  		 		 	 break;

	  		  	  		 		 	 case '4':
	  		  	  		 		 		 process_calibration(USB_Rx_buffer[4], 4);
	  		  	  		 		 	 break;

	  		  	  		 		 	 case '5':
	  		  	  		 		 		 process_calibration(USB_Rx_buffer[4], 5);
	  		  	  		 		 	 break;

	  		  	  		 		 	 case '6':
	  		  	  		 		 		 process_calibration(USB_Rx_buffer[4], 6);
	  		  	  		 		 	 break;

	  		  	  		 		 	 case '8':
	  		  	  		 		 		 error_zero_dof_7 = wrote_zero_to_dof(7);
	  		  	  		 		 		 process_calibration(USB_Rx_buffer[4], 8);
	  		  	  		 		 	 break;
	  		  	  		 		 }
	  	  		 		 		 break;

	  	  		 		 	 case'8': //  8 DoF mode choice
	  		  	  		 		 switch(USB_Rx_buffer[3])
	  		  	  		 		 {
	  		  	  		 		 	 case '1':
	  		  	  		 		 		 process_calibration(USB_Rx_buffer[4], 1);
	  		  	  		 		 	 break;

	  		  	  		 		 	 case '2':
	  		  	  		 		 		 process_calibration(USB_Rx_buffer[4], 2);
	  		  	  		 		 	 break;

	  		  	  		 		 	 case '3':
	  		  	  		 		 		 process_calibration(USB_Rx_buffer[4], 3);
	  		  	  		 		 	 break;

	  		  	  		 		 	 case '4':
	  		  	  		 		 		 process_calibration(USB_Rx_buffer[4], 4);
	  		  	  		 		 	 break;

	  		  	  		 		 	 case '5':
	  		  	  		 		 		 process_calibration(USB_Rx_buffer[4], 5);
	  		  	  		 		 	 break;

	  		  	  		 		 	 case '6':
	  		  	  		 		 		 process_calibration(USB_Rx_buffer[4], 6);
	  		  	  		 		 	 break;

	  		  	  		 		 	 case '7':
	  		  	  		 		 		 process_calibration(USB_Rx_buffer[4], 7);
	  		  	  		 		 	 break;

	  		  	  		 		 	 case '8':
	  		  	  		 		 		 process_calibration(USB_Rx_buffer[4], 8);
	  		  	  		 		 	 break;
	  		  	  		 		 }
	  	  		 		 		 break;
	  	  		 		 }
	  	  		 		 break;


	  	  		 	 case 'r': // Right arm choice  9-16 == 1-8 DoF
	  	  		 		 switch(USB_Rx_buffer[2])
	  	  		 		 {
							 case'6': //  6 DoF mode (without gripper) choice
								 switch(USB_Rx_buffer[3])
								 {
									 case '1':
										 process_calibration(USB_Rx_buffer[4], 9);
									 break;

									 case '2':
										 process_calibration(USB_Rx_buffer[4], 10);
									 break;

									 case '3':
										 process_calibration(USB_Rx_buffer[4], 11);
									 break;

									 case '4':
										 process_calibration(USB_Rx_buffer[4], 12);
									 break;

									 case '5':
										 process_calibration(USB_Rx_buffer[4], 13);
									 break;

									 case '6':
										 error_zero_dof_7 = wrote_zero_to_dof(15);
										 error_zero_dof_7 = wrote_zero_to_dof(16);
										 process_calibration(USB_Rx_buffer[4], 14);
									 break;
								 }
								 break;

	  	  		 		 	 case'7': //  7 DoF mode choice
	  		  	  		 		 switch(USB_Rx_buffer[3])
	  		  	  		 		 {
	  								 case '1':
	  									process_calibration(USB_Rx_buffer[4], 9);
	  								 break;

	  								 case '2':
	  									process_calibration(USB_Rx_buffer[4], 10);
	  								 break;

	  								 case '3':
	  									process_calibration(USB_Rx_buffer[4], 11);
	  								 break;

	  								 case '4':
	  									process_calibration(USB_Rx_buffer[4], 12);
	  								 break;

	  								 case '5':
	  									process_calibration(USB_Rx_buffer[4], 13);
	  								 break;

	  								 case '6':
	  									process_calibration(USB_Rx_buffer[4], 14);
	  								 break;

	  								 case '8':
	  									error_zero_dof_7 = wrote_zero_to_dof(15);
	  									process_calibration(USB_Rx_buffer[4], 16);
	  								 break;
	  		  	  		 		 }
	  	  		 		 		 break;

	  	  		 		 	 case'8': //  8 DoF mode choice
	  		  	  		 		 switch(USB_Rx_buffer[3])
	  		  	  		 		 {
	  								 case '1':
	  									process_calibration(USB_Rx_buffer[4], 9);
	  								 break;

	  								 case '2':
	  									process_calibration(USB_Rx_buffer[4], 10);
	  								 break;

	  								 case '3':
	  									process_calibration(USB_Rx_buffer[4], 11);
	  								 break;

	  								 case '4':
	  									process_calibration(USB_Rx_buffer[4], 12);
	  								 break;

	  								 case '5':
	  									process_calibration(USB_Rx_buffer[4], 13);
	  								 break;

	  								 case '6':
	  									process_calibration(USB_Rx_buffer[4], 14);
	  								 break;

	  								 case '7':
	  									process_calibration(USB_Rx_buffer[4], 15);
	  								 break;

	  								 case '8':
	  									process_calibration(USB_Rx_buffer[4], 16);
	  								 break;
	  		  	  		 		 }
	  	  		 		 		 break;
	  	  		 		 }
	  	  		 		 break;
	  	  		 }
				 clearBufferAndCounter();
				 clearUsbBuffers();
				 break;

			 case 'r':
	  		 		 switch(USB_Rx_buffer[1])
	  		 		 {
						 case '1':
							 // Function with communication with force sensor pcb
							 if (readForseSensor() == 1)
							 {
								 stop_motor_counter=0;
								 set_new_force();
								 readADCchannels();
								 is_min_max_calibrated();
								 calibration_ADC_values();
								 memcpy(USB_Tx_buffer + 0, (uint8_t*)(&adcBuffer), sizeof(adcBuffer));
								 memcpy(USB_Tx_buffer + sizeof(adcBuffer), (uint8_t*)(&force_sensor_4_value), sizeof(force_sensor_4_value));
								 memcpy(USB_Tx_buffer + sizeof(adcBuffer) + sizeof(force_sensor_4_value), (uint8_t*)(&start_dataset_collection_flag), sizeof(start_dataset_collection_flag));
								 memcpy(USB_Tx_buffer + sizeof(adcBuffer) + sizeof(force_sensor_4_value) + sizeof(start_dataset_collection_flag), (uint8_t*)(&sense_flag), sizeof(sense_flag));
								 while (CDC_Transmit_FS(USB_Tx_buffer, sizeof(adcBuffer) + sizeof(force_sensor_4_value) + sizeof(start_dataset_collection_flag) + sizeof(sense_flag)) == USBD_BUSY)
									 ; // Wait for end of transmission
							 }
							 else
							 {
								 LL_mDelay(1);
								 if (readForseSensor() == 1)
								 {
									 stop_motor_counter=0;
									 set_new_force();
									 readADCchannels();
									 is_min_max_calibrated();
									 calibration_ADC_values();
									 memcpy(USB_Tx_buffer + 0, (uint8_t*)(&adcBuffer), sizeof(adcBuffer));
									 memcpy(USB_Tx_buffer + sizeof(adcBuffer), (uint8_t*)(&force_sensor_4_value), sizeof(force_sensor_4_value));
									 memcpy(USB_Tx_buffer + sizeof(adcBuffer) + sizeof(force_sensor_4_value), (uint8_t*)(&start_dataset_collection_flag), sizeof(start_dataset_collection_flag));
									 memcpy(USB_Tx_buffer + sizeof(adcBuffer) + sizeof(force_sensor_4_value) + sizeof(start_dataset_collection_flag), (uint8_t*)(&sense_flag), sizeof(sense_flag));
									 while (CDC_Transmit_FS(USB_Tx_buffer, sizeof(adcBuffer) + sizeof(force_sensor_4_value) + sizeof(start_dataset_collection_flag) + sizeof(sense_flag)) == USBD_BUSY)
										 ; // Wait for end of transmission
								 }
							 }
							 break;

						 case '2':
							 readADCchannels();
							 is_min_max_calibrated();
							 calibration_ADC_values();
							 memcpy(USB_Tx_buffer + 0, (uint8_t*)(&adcBuffer), sizeof(adcBuffer));
							 memcpy(USB_Tx_buffer + sizeof(adcBuffer), (uint8_t*)(&start_dataset_collection_flag), sizeof(start_dataset_collection_flag));
							 memcpy(USB_Tx_buffer + sizeof(adcBuffer) + sizeof(start_dataset_collection_flag), (uint8_t*)(&sense_flag), sizeof(sense_flag));
							 while (CDC_Transmit_FS(USB_Tx_buffer, sizeof(adcBuffer) + sizeof(start_dataset_collection_flag) + sizeof(sense_flag)) == USBD_BUSY)
								 ; // Wait for end of transmission
							 break;
	  		 		 }

				 clearBufferAndCounter();
				 clearUsbBuffers();
				 break;

			 case 'e':
				 erase_flash(FLASH_SECTOR_6);
				 erase_flash(FLASH_SECTOR_7);
				 clearBufferAndCounter();
				 clearUsbBuffers();
				 break;

			 case 'x':
				 load_calibration_values();
				 memcpy(USB_Tx_buffer + 0, (uint8_t*)(&CCW_limits), sizeof(CCW_limits));
				 memcpy(USB_Tx_buffer + sizeof(CW_limits), (uint8_t*)(&CW_limits), sizeof(CW_limits));
				 while (CDC_Transmit_FS(USB_Tx_buffer, sizeof(CCW_limits) + sizeof(CW_limits)) == USBD_BUSY)
					 ; // Wait for end of transmission
				 clearBufferAndCounter();
				 clearUsbBuffers();
				 break;

			 case 's':
//				 stop_motor();
				 memset(USB_Rx_buffer, 0, sizeof(USB_Rx_buffer)); // Clear USB Rx buffer
				 break;

			 default:
				 stop_motor_counter ++;
				 if (stop_motor_counter>=2000)
				 {
					 stop_motor_counter=3000;
					 stop_motor();
				 }
				 information_leds_activation();
				 clearUsbBuffers();
				 clearBufferAndCounter();
				 continue;
		  }
    /* USER CODE END WHILE */

    /* USER CODE BEGIN 3 */
  }
  /* USER CODE END 3 */
}

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


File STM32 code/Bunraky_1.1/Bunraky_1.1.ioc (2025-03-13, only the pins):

Mcu.UserName=STM32F401RETx
PA0-WKUP.Signal=ADCx_IN0
PA1.Signal=ADCx_IN1
PA11.Signal=USB_OTG_FS_DM
PA12.Signal=USB_OTG_FS_DP
PA13.Signal=SYS_JTMS-SWDIO
PA14.Signal=SYS_JTCK-SWCLK
PA15.Signal=S_TIM2_CH1_ETR
PA2.Signal=ADCx_IN2
PA3.Signal=ADCx_IN3
PA4.Signal=ADCx_IN4
PA5.Signal=ADCx_IN5
PA6.Signal=ADCx_IN6
PA7.Signal=ADCx_IN7
PA8.GPIO_Label=Buzzer
PA8.Signal=GPIO_Output
PB0.Signal=ADCx_IN8
PB1.Signal=ADCx_IN9
PB12.GPIO_Label=Sense_Lvl_1
PB12.Signal=GPIO_Output
PB13.GPIO_Label=Sense_Lvl_2
PB13.Signal=GPIO_Output
PB14.GPIO_Label=Sense_Lvl_3
PB14.Signal=GPIO_Output
PB15.GPIO_Label=EXTI15_10_Selecting_the_sensitivity_mode
PB15.Signal=GPXTI15
PB2.GPIO_Label=BOOT1
PB2.Signal=GPIO_Input
PB3.GPIO_Label=En_left_motor
PB3.Signal=GPIO_Output
PB4.Signal=S_TIM3_CH1
PB5.GPIO_Label=Dir_left_motor
PB5.Signal=GPIO_Output
PB8.GPIO_Label=EXTI9_5_start_dataset_collection
PB8.Signal=GPXTI8
PB9.GPIO_Label=start_dataset_collection_led
PB9.Signal=GPIO_Output
PC0.Signal=ADCx_IN10
PC1.Signal=ADCx_IN11
PC10.GPIO_Label=En_right_motor
PC10.Signal=GPIO_Output
PC11.GPIO_Label=Dir_right_motor
PC11.Signal=GPIO_Output
PC2.Signal=ADCx_IN12
PC3.Signal=ADCx_IN13
PC4.Signal=ADCx_IN14
PC5.Signal=ADCx_IN15
PC6.Signal=USART6_TX
PC7.Signal=USART6_RX
PC8.GPIO_Label=RE_DE
PC8.Signal=GPIO_Output

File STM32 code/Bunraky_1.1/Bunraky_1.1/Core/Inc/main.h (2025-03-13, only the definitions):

#define BOOT1_Pin LL_GPIO_PIN_2
#define BOOT1_GPIO_Port GPIOB
#define Sense_Lvl_1_Pin LL_GPIO_PIN_12
#define Sense_Lvl_1_GPIO_Port GPIOB
#define Sense_Lvl_2_Pin LL_GPIO_PIN_13
#define Sense_Lvl_2_GPIO_Port GPIOB
#define Sense_Lvl_3_Pin LL_GPIO_PIN_14
#define Sense_Lvl_3_GPIO_Port GPIOB
#define EXTI15_10_Selecting_the_sensitivity_mode_Pin LL_GPIO_PIN_15
#define EXTI15_10_Selecting_the_sensitivity_mode_GPIO_Port GPIOB
#define EXTI15_10_Selecting_the_sensitivity_mode_EXTI_IRQn EXTI15_10_IRQn
#define RE_DE_Pin LL_GPIO_PIN_8
#define RE_DE_GPIO_Port GPIOC
#define Buzzer_Pin LL_GPIO_PIN_8
#define Buzzer_GPIO_Port GPIOA
#define En_right_motor_Pin LL_GPIO_PIN_10
#define En_right_motor_GPIO_Port GPIOC
#define Dir_right_motor_Pin LL_GPIO_PIN_11
#define Dir_right_motor_GPIO_Port GPIOC
#define En_left_motor_Pin LL_GPIO_PIN_3
#define En_left_motor_GPIO_Port GPIOB
#define Dir_left_motor_Pin LL_GPIO_PIN_5
#define Dir_left_motor_GPIO_Port GPIOB
#define EXTI9_5_start_dataset_collection_Pin LL_GPIO_PIN_8
#define EXTI9_5_start_dataset_collection_GPIO_Port GPIOB
#define EXTI9_5_start_dataset_collection_EXTI_IRQn EXTI9_5_IRQn
#define start_dataset_collection_led_Pin LL_GPIO_PIN_9
#define start_dataset_collection_led_GPIO_Port GPIOB

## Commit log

2025-02-26 main PCB
    [Drill_NPTH_Through.DRL, Drill_PTH_Through.DRL, Drill_PTH_Through_Via.DRL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]
2025-03-12 New branch for pages
    [Echo main PCB Bill Of Materials.xlsx, Potentiometers smd BOM.xlsx]
2025-03-13 Main code + mc code + electronics
    [BOM Force sensor PCB.xlsx, Echo main PCB Bill Of Materials.xlsx, Potentiometers smd BOM.xlsx]
2025-03-14 Restructure + renaming
    [BOM Force sensor PCB.xlsx, Echo main PCB Bill Of Materials.xlsx, Potentiometers smd BOM.xlsx]
2025-03-24 3D models
    [1111.100.000 - Aluminum frame.prt, 1111.100.002 - Aluminum profile.prt, 1111.100.004 - Aluminum profile.prt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]
2025-03-26 new models
    [ECHO.000.000.000 - Teleoperation System with Force Feedback.prt, ECHO.000.004.000 - Joystick right.prt, ECHO.000.014.100 - Trigger.prt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]
2025-07-04 force sensor code

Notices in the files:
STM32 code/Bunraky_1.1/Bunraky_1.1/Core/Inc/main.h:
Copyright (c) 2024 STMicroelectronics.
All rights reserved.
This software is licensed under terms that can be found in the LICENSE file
